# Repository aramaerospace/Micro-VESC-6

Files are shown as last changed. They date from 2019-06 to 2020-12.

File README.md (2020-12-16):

# Micro-VESC-6
Micro VESC-6:  44mmx34mm PCB packs the VESC 6 with 6xPowerTDFN FETS. 3.3V regulator only.
Update: I have been working with VESC for the last few years and would love to revisit the Micro-VESC-6 design. The one which is published currently can be improved a lot, to say the least. 
I plan to publish much better version within the next 3-5 months. Thanks!

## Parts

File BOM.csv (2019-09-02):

R31 | 1k | ESR03EZPJ102
R32,33 | 220R | ESR03EZPJ221
Q1-Q6 |  | NTMFS5C604NLT1G
R1,R34,R35,R8,R10,R15,R17 | 2k2 | RC0603FR-072K2L
D3 | LED BLE | LB Q39G-L2OO-35-1
D4 | GREEN | LTST-C191KGKT
D5 | RED | LTST-C191KRKT
R29,R30 | 22R | ERJ-3EKF22R0V
J8,J8*(on PCB only) | COMM1,COMM2 | 68683-303LF
C2,C8 | 15pF | GRM1885C2A150JA01D
C7,C25 | 0.1uF | 06035G104ZAT2A
C1,C3,C4,C5,C6,C9,C10,C11,C12,C13,C14,C16,C29,C31,C38,C39,C40 | 2.2uF | GRM188R6YA225MA12D
X1 |  | ABM3B-8.000MHZ-10-1-U-T
R2,R5,R22 | 10k | RR1220P-103-D
R3 | 32.4k | ERJ-3EKF3242V
R4 | 147k | ERJ-3EKF1473V
R6 | 732k | CRCW0603732KFKEA
C15 | 750p | CL10B751KB8NNNC
C18 | 6.8p | CGA3E2NP02A6R8D080AA
C17 | 0.022uF | CL10B223KB8NNWC
C20 | 6.8nF | 06035C682J4T2A
C22,C27,C28 | 220nF | GCM188R71H224KA64D
R7,R9,R14,R16 | 39k | AC0603FR-0739KL
R21 | NTC 10k | B57330V2103F260
R18,R19,R23,R24,R26,R27 | 4R7 | RK73B1JTTD4R7J
C19,C21,C24 | 4.7nF | CL10B472KC8NNNC
R11,R12,R13 | 100R | RC0603FR-07100RL
R20,R25,R28,R36(on PCB only) | .005R | WSLF2512L5000FEA
U3,U4,U5 |  | AD8418WBRMZ
U1 |  | STM32F405RGT6
U2 |  | DRV8301DCAR
C23,C26,C32,C33,C34,C35,C36,C37 | 4.7uF | C1206C475K5PACTU
C59,C60,C61,C62,C63 | 10uF | UMK316BBJ106ML-T
C45 | 22uF | CL21A226MOCLRNC
L1 | 47uH | TYS5040470M-10
D1 |  | SMD26PL-TP

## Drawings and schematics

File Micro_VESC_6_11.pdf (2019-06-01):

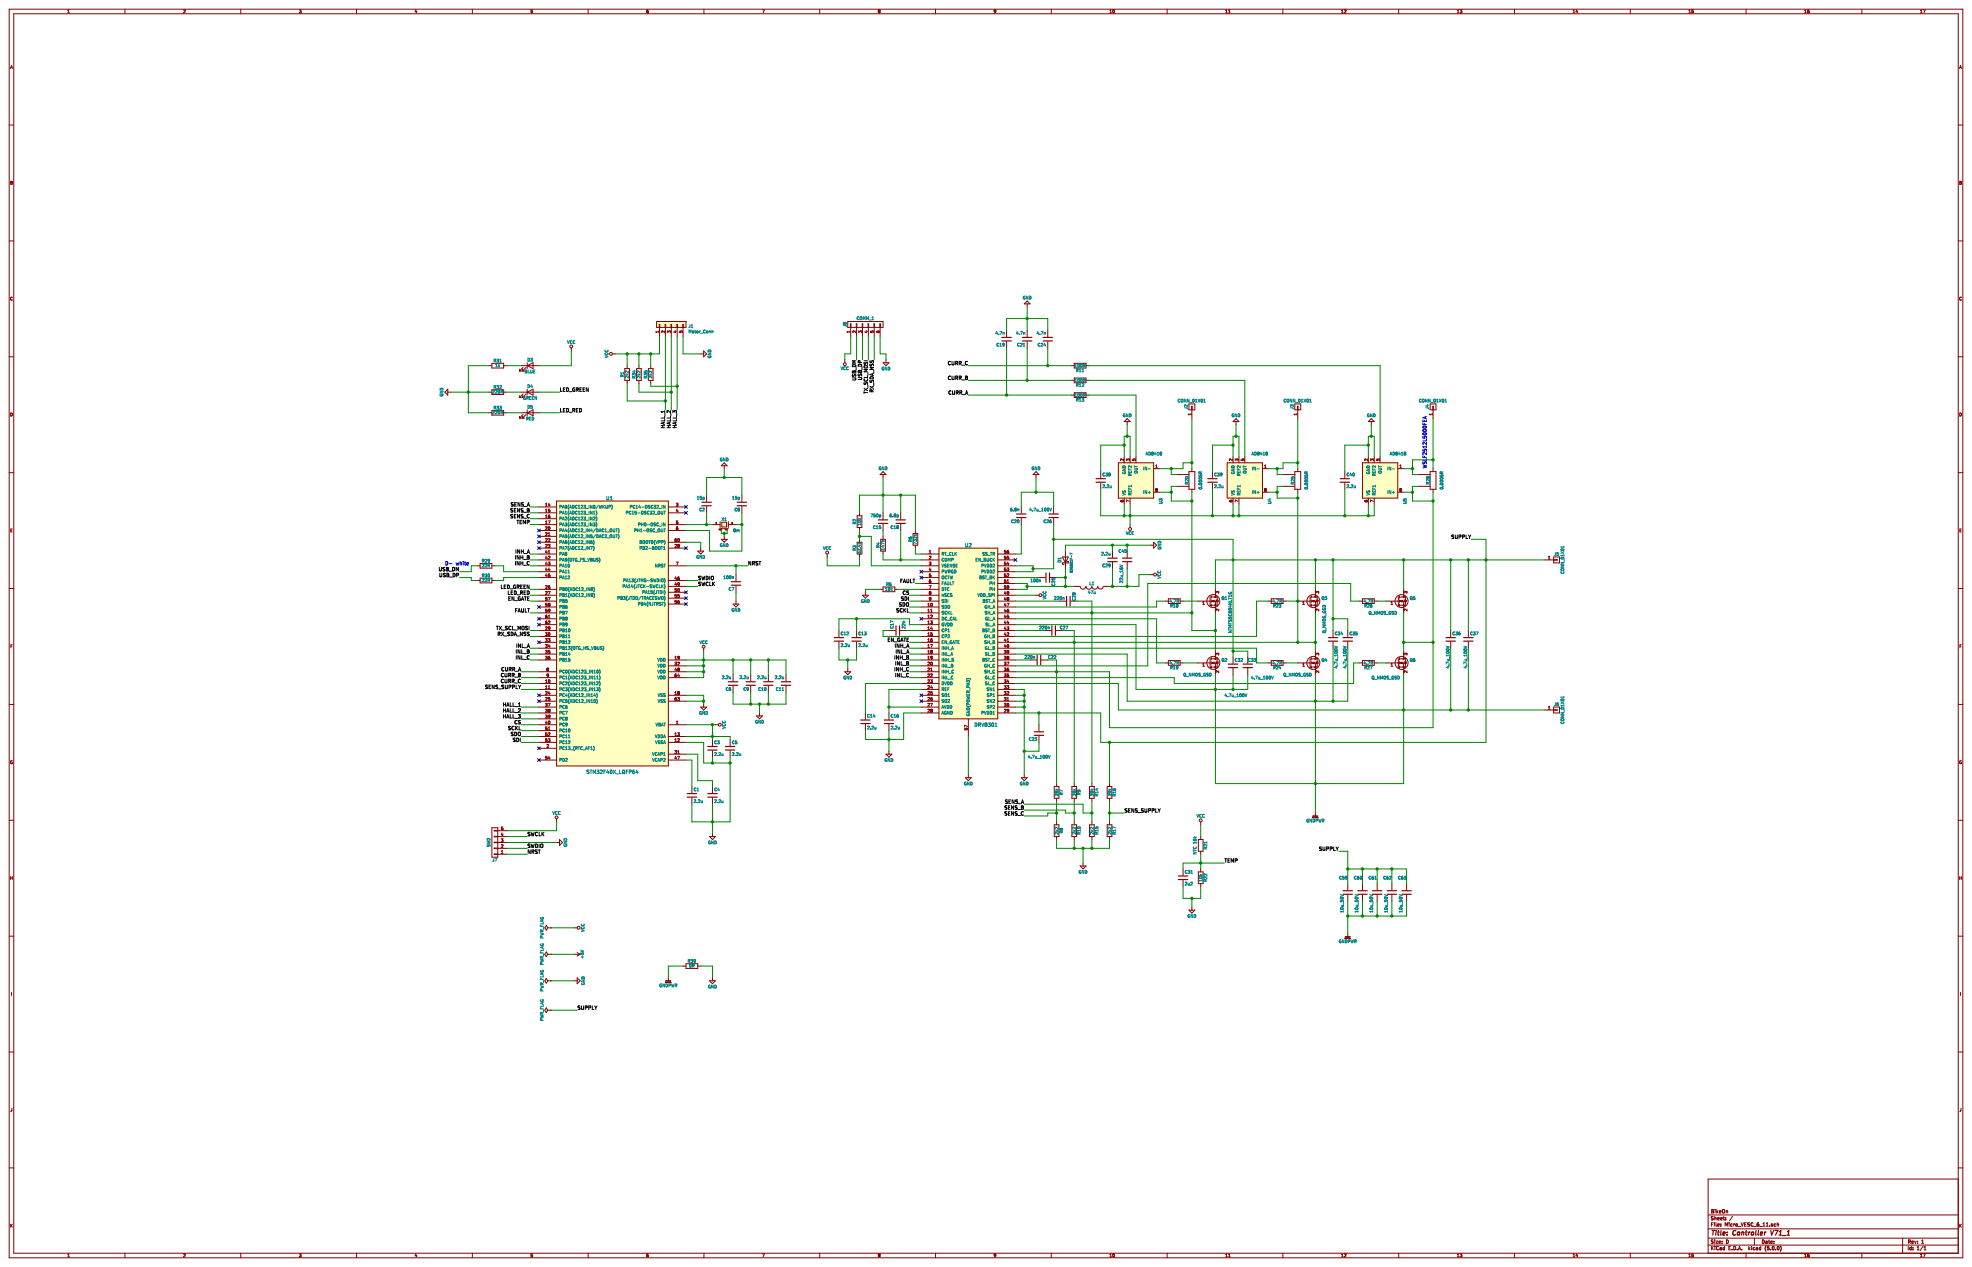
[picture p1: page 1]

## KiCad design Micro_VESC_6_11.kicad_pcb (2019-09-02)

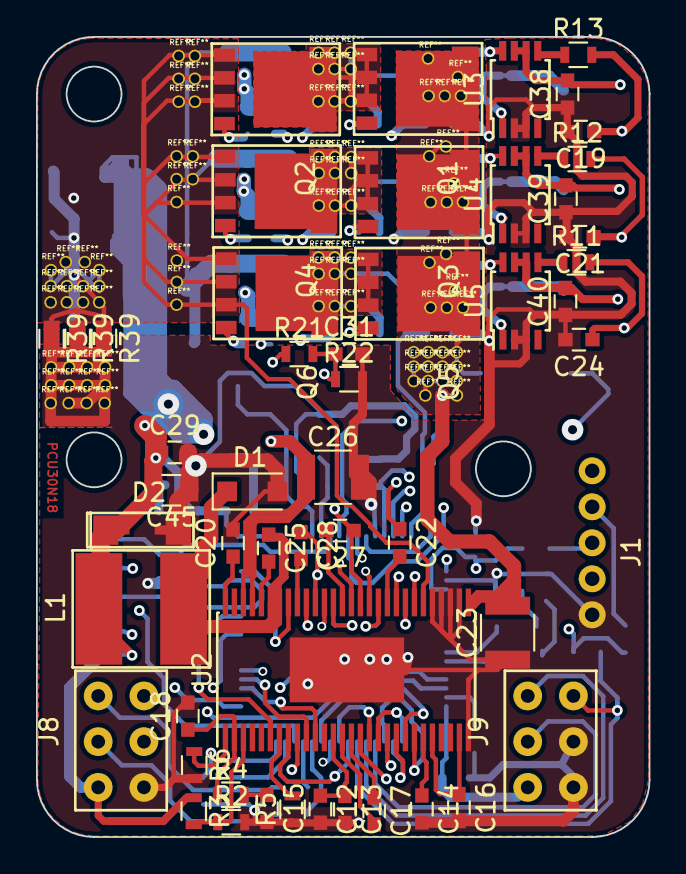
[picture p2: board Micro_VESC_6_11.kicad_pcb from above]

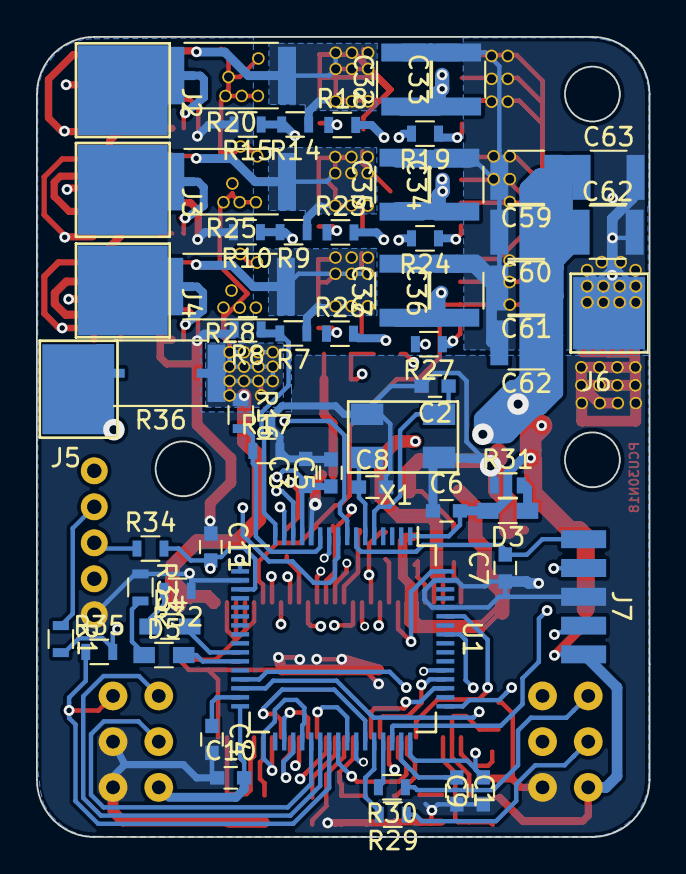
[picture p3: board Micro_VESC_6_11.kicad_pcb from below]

Board: 4 copper layers, 34.0 x 44.5 mm, 112 parts (60 on the bottom side), 82 nets.

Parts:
C1, C3, C4, C5, C6, C9, C10, C11, C12, C13, C14, C16, C29, C38, C39, C40: 2.2u; C_0603
C2, C8: 15p; C_0603
C7, C25: 100n; C_0603
C15: 750p; C_0603
C17: 22n; C_0603
C18: 6.8p; C_0603
C19, C21, C24: 4.7n; C_0603
C20: 6.8n; C_0603
C22, C27, C28: 220n; C_0603
C23, C26, C32, C33, C34, C35, C36, C37: 4.7u_100V; C_1210
C31: 2u2; C_0603
C45: 22u_16V; C_0805
C59, C60, C61, C62, C62#2, C63: 10u_50V; C_1210
D1: B260S1F-7; D_SOD-123F
D2: TVS 5V; DO-214AC_SOD-323
D3: BLUE; R_0603_HandSoldering
D4: GREEN; R_0603_HandSoldering
D5: RED; R_0603_HandSoldering
J1: Motor_Conn; Wire_Pad_Thru_1x5
J2, J3, J4, J5, J6: CONN_01X01; PAD_5x5mm
J7: SWD; SWD_5PIN
J8: COMM_1; 2x6_2_54MezConn
J9: COMM_2; 2x6_2_54MezConn
L1: 47u; Inductor_SRR6038-220Y
Q1: NTMFS5C604NLT1G; SO8FL_UNIVERSAL
Q2, Q3, Q4, Q5, Q6: Q_NMOS_GSD; SO8FL_UNIVERSAL
R1, R8, R10, R15, R17, R34, R35: 2k2; R_0603
R2, R5, R22: 10k; R_0603
R3: 32.4k; R_0603
R4: 147k; R_0603
R6: 732k; R_0603
R7, R9, R14, R16: 39k; R_0603
R11, R12, R13: 100R; R_0603
R18, R19, R23, R24, R26, R27: 4.7R; R_0603
R20, R25, R28, R36: 0.0005R; R_2512_SHUNT
R21: NTC 10k; R_0603
R29, R30: 22R; R_0603
R31: 1k; R_0603
R32, R33: 220R; R_0603
R39, R39#2, R39#3: 0R; R_0603
U1: STM32F40X_LQFP64; LQFP-64_10x10mm_Pitch0.5mm
U2: DRV8301; HTSSOP-56-1EP_6.1x14mm_Pitch0.5mm
U3, U4, U5: AD8418; TSSOP-8_3x3mm_Pitch0.65mm
X1: 8m; CRYSTAL_ABM3B

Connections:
/CS: U1.40, U2.8
/CURR_A: C19.1, R13.2, U1.8
/CURR_B: C21.1, R12.2, U1.9
/CURR_C: C24.1, R11.2, U1.10
/EN_GATE: U1.57, U2.16
/FAULT: U1.59, U2.6
/HALL_1: J1.2, J9.2, R1.1, U1.37
/HALL_2: J1.3, J9.3, R34.1, U1.38
/HALL_3: J1.4, J9.4, R35.1, U1.39
/INH_A: U1.41, U2.17
/INH_B: U1.42, U2.19
/INH_C: U1.43, U2.21
/INL_A: U1.34, U2.18
/INL_B: U1.35, U2.20
/INL_C: U1.36, U2.22
/LED_GREEN: D4.2, U1.26
/LED_RED: D5.2, U1.27
/NRST: C7.2, J7.1, U1.7
/RX_SDA_NSS: J8.5, U1.30
/SCKL: U1.51, U2.11
/SDI: U1.53, U2.9
/SDO: U1.52, U2.10
/SENS_A: R14.2, R15.1, U1.14
/SENS_B: R9.2, R10.1, U1.15
/SENS_C: R7.2, R8.1, U1.16
/SENS_SUPPLY: R16.2, R17.1, U1.11
/SUPPLY: C23.2, C26.1, C32.1, C33.1, C34.1, C35.1, C36.1, C37.1, C59.1, C60.1, C61.1, C62.1, C62#2.1, C63.1, J5.1, Q1.3, Q3.3, Q5.3, R16.1, R36.1, R36.2, R36.3, R36.4, U2.29, U2.53, U2.54
/SWCLK: J7.4, U1.49
/SWDIO: J7.2, U1.46
/TEMP: C31.1, R21.2, R22.1, U1.17
/TX_SCL_MOSI: J8.4, U1.29
/USB_DM: J8.2, R29.1
/USB_DP: J8.3, R30.1
GND: C1.2, C2.2, C3.2, C4.2, C5.2, C6.1, C7.1, C8.2, C9.1, C10.1, C11.1, C12.2, C13.2, C14.2, C15.2, C16.2, C18.2, C19.2, C20.2, C21.2, C23.1, C24.2, C26.2, C29.2, C31.2, C38.1, C39.1, C40.1, C45.1, D1.2, D2.2, J1.5, J7.3, J8.6, J9.5, J9.6, R2.2, R5.1, R6.2, R8.2, R10.2, R15.2, R17.2, R22.2, R31.1, R32.1, R33.1, R39.2, R39#2.2, R39#3.2, U1.12, U1.18, U1.60, U1.63, U2.28, U2.30, U2.31, U2.32, U2.33, U2.57, U3.2, U3.3, U4.2, U4.3, U5.2, U5.3, X1.2, X1.4
GNDPWR: C32.2, C33.2, C34.2, C35.2, C36.2, C37.2, C59.2, C60.2, C61.2, C62.2, C62#2.2, C63.2, J6.1, Q2.2, Q4.2, Q6.2, R39.1, R39#2.1, R39#3.1, U2.34, U2.39, U2.44
unnamed: C1.1, U1.47
unnamed: C2.1, U1.5, X1.1
unnamed: C4.1, U1.31
unnamed: C8.1, U1.6, X1.3
unnamed: C12.1, C13.1, U2.13
unnamed: C14.1, U2.23
unnamed: C15.1, R4.2
unnamed: C16.1, U2.24, U2.27
unnamed: C17.1, U2.15
unnamed: C17.2, U2.14
unnamed: C18.1, R4.1, U2.2
unnamed: C20.1, U2.56
unnamed: C22.1, Q5.2, Q6.3, R7.1, R28.1, R28.3, U2.36, U5.8
unnamed: C22.2, U2.38
unnamed: C25.1, D1.1, L1.2, U2.50, U2.51
unnamed: C25.2, U2.52
unnamed: C27.1, Q3.2, Q4.3, R9.1, R25.1, R25.3, U2.41, U4.8
unnamed: C27.2, U2.43
unnamed: C28.1, Q1.2, Q2.3, R14.1, R20.1, R20.3, U2.46, U3.8
unnamed: C28.2, U2.48
unnamed: D3.1, R31.2
unnamed: D4.1, R32.2
unnamed: D5.1, R33.2
unnamed: J2.1, R20.2, R20.4, U3.1
unnamed: J3.1, R25.2, R25.4, U4.1
unnamed: J4.1, R28.2, R28.4, U5.1
unnamed: Q1.1, R18.1
unnamed: Q2.1, R19.1
unnamed: Q3.1, R23.1
unnamed: Q4.1, R24.1
unnamed: Q5.1, R26.1
unnamed: Q6.1, R27.1
unnamed: R2.1, R3.2, U2.3
unnamed: R5.2, U2.7
unnamed: R6.1, U2.1
unnamed: R11.1, U5.5
unnamed: R12.1, U4.5
unnamed: R13.1, U3.5
unnamed: R18.2, U2.47
unnamed: R19.2, U2.45
unnamed: R23.2, U2.42
unnamed: R24.2, U2.40
unnamed: R26.2, U2.37
unnamed: R27.2, U2.35
unnamed: R29.2, U1.44
unnamed: R30.2, U1.45
VCC: C3.1, C5.1, C6.2, C9.2, C10.2, C11.2, C29.1, C38.2, C39.2, C40.2, C45.2, D2.1, D3.2, J1.1, J7.5, J8.1, J9.1, L1.1, R1.2, R3.1, R21.1, R34.2, R35.2, U1.1, U1.13, U1.19, U1.32, U1.48, U1.64, U2.49, U3.6, U3.7, U4.6, U4.7, U5.6, U5.7

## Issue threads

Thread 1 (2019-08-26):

Has this been tested?

john--, 2019-08-26:
Looks great. Just curious if it's been tested?

aramaerospace, 2019-08-26:
Yes, it has been tested, worked fine. Here is a picture of an assembled board.

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

john--, 2019-08-26:
Wow, great work!
I'm tempted to build this thing. Where did you order your components?

john--, 2019-09-01:
@aramaerospace sorry for the delay, that would actually be great! I had the PCB made at JLCPCB, my goto place. Shipping will take some time though, so I'm in rush to get my BOM ordered.

aramaerospace, 2019-09-02:
Added the BOM, hope this helps. I've also corrected some issues on the PCB: some of the connections from DRV8301 to the FETs where messed up. It is corrected now. If you've ordered your boards, I'd advice to re-order them. Sorry for that!

john--, 2019-09-02:
Oh nice, thanks! Oh don't worry about it, PCBs aren't terribly expensive. Really appreciate your work here!
